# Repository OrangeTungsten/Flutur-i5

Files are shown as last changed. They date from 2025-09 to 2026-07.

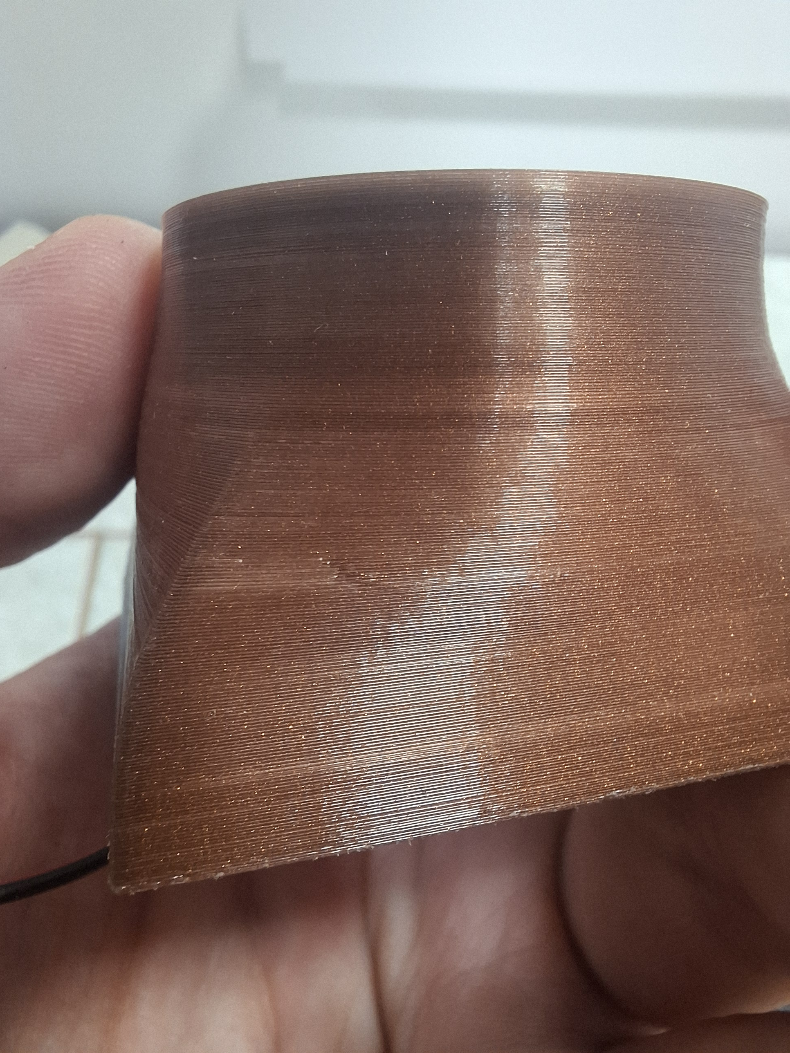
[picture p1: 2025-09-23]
Images/Printing results/20250920_120809.jpg

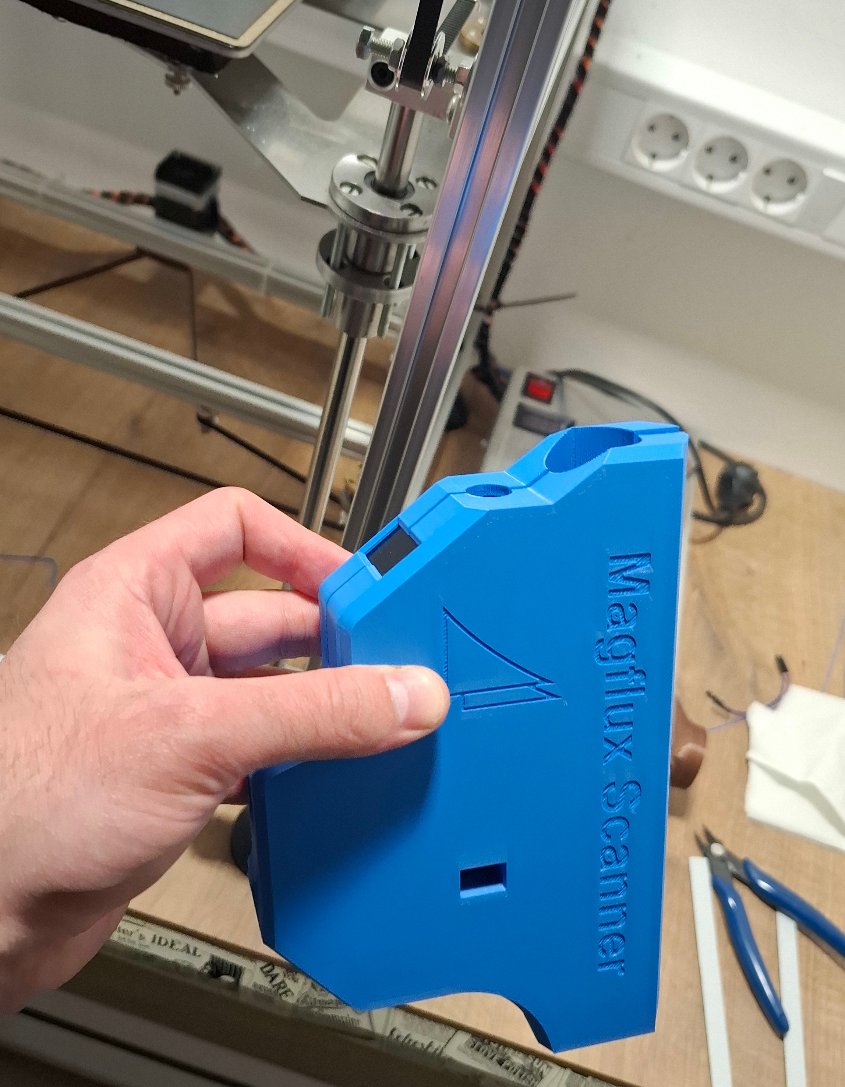
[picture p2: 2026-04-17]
Images/Printing results/11.jpg

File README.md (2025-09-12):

# Flutur-i5
Flutur Logo

# Introduction
Flutur i5 is an open-source 3D printer project, created by an enthusiast for the wider maker community. It is designed to inspire and support fellow makers and DIY lovers. The idea behind Flutur is to build a stable, reliable and flexibile 3D printer that is affordable, easy to assemble, operate and modify.

This is a 3D printer featuring a Cartesian-style positioning system, driven by three two-phase stepper motors: belt-driven on the X and Y axes, and lead screw-driven on the Z axis; all guided by linear bearings on Ø12 stainless steel rods. The entire system is assembled into a rigid rectangular (box-type) aluminum frame, made of 20 x 20 mm slot profile members. The printable volume is 285 × 300 × 300 mm (X × Y × Z).

# Bill of Materials (BOM)
The BOM.xls file contains materials with quantities needed for this project. Names of components follow provided assembly drawings. All measures are given in milimeters. 

Printable components could be FDM 3D printed with basic PLA filament, even the extruder plate. Both portal plates could be made of acrylics or aluminum. Hotend requires active cooling. Workpiece cooling is also recommended. 

In this version of the project, the control system consists of an _MKS Robin Nano v1.2_ control board, together with _TMC2208_ stepper drivers and a _MKS TFT35 v1.0_ display. The motion system is driven by four NEMA17 17HS8401 stepper motors. Power supply must provide at least 30 A at 12 V DC. The Flutur i5 project does not provide instructions for wiring or electrical instalation in general. The proper wiring, operation and handling of these components are defined by their respective manufacturers, and their official documentation should be followed.

The control board runs on [Marlin v2.1.2.5](https://github.com/MarlinFirmware/Marlin/tree/lts-2.1.2) firmware. Configuration files are given.

## 3rd Party Disclaimer

This project is designed to be compatible with certain commercially available components from third-party manufacturers. This project does not distribute, reproduce, or claim ownership of any third-party models. Users requiring detailed technical information, specifications, or official design files of these components, should obtain them directly from the respective manufacturers’ official sources. This project also uses a combination of widely available off-the-shelf components (e.g. standard bearings and fasteners). While references to such parts are made in the design, no third-party models are included in this repository.

The printer can also be realized with other solutions, depending on the builder’s preferences and requirements. In that case, modifications of certain parts may be required, such as adapting or redesigning mounting positions to fit the new hardware.

List of fully compatibile 3rd party components with their webistes:

[Stepper Motor NEMA17 17HS8401](https://www.hanpose.com/product-17hs8401-18a--52ncm-18-degree--linear--motor-12v-electric-toys-and-appliances-for-3d-printer-nema-17-stepper-motor)

[Controler board MKS Robin Nano v1.2](https://makerbase3d.com/product/mks-robin-nano-v1-2/)

[Display MKS TFT35 V1.0](https://makerbase3d.com/product/mks-robin-nano-v1-2/)

[Filament Feeder Creality MK8 style](https://www.crealityofficial.co.uk/products/full-metal-extruder-with-capricorn-tubing)

[Hotend E3D V6 type](https://e3d-online.com/products/v6-all-metal-hotend?_pos=5&_sid=d5b714545&_ss=r&variant=40923457486907)

[Sensor BL Touch v3.1](https://www.antclabs.com/bltouch)

[Endstop Cherry DB2 Microswitch](https://platinum-international.store/platinum-international/switches/position-switches/cherry-db2-subminiature-switch/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)

# Safety and Fire Hazard Disclaimer

3D printers are devices that operate with electricity and heat, and therefore must be considered potentially hazardous. Electrical wiring and installation on this device should only be performed by individuals with the appropriate knowledge and experience. Special attention must be given to all electrical connections, especially joints and connectors.

The author of this project assumes no responsibility or liability for any potential damage, injury, or loss resulting from the reproduction, assembly, or use of this device. All responsibility rests with the builder/user.

Building your own 3D printer can be a fun and rewarding experience, but please remember: safety comes first. Always double-check your wiring, use quality connectors, and don’t leave the printer unattended during operation. Treat this project as both a learning journey and a responsibility — careful assembly and mindful use will make your device safer and more reliable.

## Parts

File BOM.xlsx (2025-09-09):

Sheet: All Total
Item | Qty.
Aluminum Profiles
Slot Profile 2020 l = 525 | 4
Slot Profile 2020 l = 410 | 6
Slot Profile 2020 l = 480 | 5
Profile Connectors
Slot Profile Corner Connector | 4
Slot Profile Angle Connector | 6
Slot Profile Angle Connector-Short | 4
Slot Profile Plate Connector | 8
External Angle Connector | 12
T Slot Nut 2020 M5 | 89
Adjustable Leg M5 | 4
Motion
Stepper Motor NEMA17 17HS8401 | 4
Synchronous Pulley GT2-20t x 6 | 6
Synchronous Pulley GT2-40t x 6 | 2
Idler Pulley GT2-20t x 6 | 9
Synchronous Loop Belt GT2-158 x 6 | 1
Synchronous Loop Belt GT2-1220 x 6 | 1
Synchronous Belt GT2-1116 x 6 | 1
Synchronous Belt GT2-970 x 6 | 2
Ball Bearing F686-2RS 6 x 13 x 5 | 2
Y Shaft Φ6 x 515 | 1
Linear Guide Support SK12 | 16
Linear Guide Φ12 x 370 | 4
Linear Guide Φ12 x 446 | 2
Linear Guide Φ12 x 375 | 2
Linear Bearing Block SC12UU | 6
Linear Bearing Block LMF12UU | 4
Ball Bearing with Housing KP08 | 2
Lead Screw T10 x 2 | 2
Lead Nut T10 x 2 | 2
Fasteners
Cross Head Screw M2 x 14 | 4
Nut M2 | 4
Washer 2.5x5x0.5 | 4
Cross Head Screw M3 x 6 | 44
Cross Head Screw M3 x 12 | 18
Cross Head Countersink Bolt M3 x 10 | 12
Cross Head Countersink Bolt M3 x 40 | 4
Nut M3 | 18
Knob Nut M3 | 4
Insert Nut M3 x 3 | 30
Washer 3.5 x 7 x 0.5 | 22
Flat Head Bolt M4 x 10 | 23
Nut M4 | 21
Insert Nut M4 x 4 | 4
Washer 4.5 x 9 x 0.8 | 19
Cross Head Bolt M5 x 10 | 49
Cross Head Bolt M5 x 12 | 62
Cross Head Screw M5 x 35 | 2
Socket Head Bolt M5 x 30 | 8
Hexagonal Head Bolt M5 x 35 | 11
Nut M5 | 29
Washer 5.5 x 10 x 1.5 | 8
Washer 5.5x15x1.5 | 8
Washer 5.5 x 18 x 1.5 | 11
Idler Pulley Positioner | 22
Compression Spring 20 x 5 x 5 | 4
Printables
Extruder plate | 1
Stepper Motor Bracket | 2
Portal Plate - Right | 1
Portal Plate - Left | 1
Y Shaft Bearing Bracket | 2
Cable Bracket - Right | 1
Cable Bracket - Left | 1
Cable Bracket - Extruder | 1
Y Endstop Spacer | 1
Belt Pin | 4
Bl Touch Bracket | 1
Housing Leg | 4
Front Panel Holder | 1
Display Panel | 1
Side Fan Holder | 2
Upper Fan Holder | 1
Electro-mechanical
Endstop Cherry DB2 Microswitch | 2
BL Touch v3.1 | 1
Main Switch 250V 10A 22 x 28 | 1
Reset Push-button Ø6 | 1
Fan Ø40 | 4
Power Supply 320 W | 1
Controller Board | 1
Display | 1
Sheet metal work
Filament Feeder Plate | 1
Heated Bed Plate | 1
Housing Base | 1
Housing Lid | 1
Material Deposition
Filament Feeder MK8-style | 1
Teflon Tube Φ1.75 x 120 | 1
Hotend E3D V6 type | 1
Aluminum Heated Bed 310 x 310 | 1
Cable management
Flat Bar Connector 20 x 458.5 x 4 | 1
X Cable Chain Rail 10 x 15 x 400 | 1
Y Cable Chain Rail 10 x 15 x 400 | 2
Z Cable Chain Rail 10 x 15 x 400 | 1
Cables
2 x 0.14 (20 AWG) x 2400 | 1
4 x 0.14 (26 AWG) x 1600 | 1
4 x 0.25 (23 AWG) x 1600 | 1
2 x 0.35 (22 AWG) x 3200 | 1
4 x 0.5 (20 AWG) x 3800 | 1
2 x 0.75 (18 AWG) x 1600 | 1
2 x 2.5 (14 AWG) x 800 | 1

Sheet: Cables
No. | Purpose | Cores | CS [mm2] | AWG | Qty. | Length [m] | Note
1 | Stepper E | 4 | 0.50 | 20 | 1 | 1.6
2 | Heater - E | 2 | 0.75 | 18 | 1 | 1.6 | Heat-resistant insulation
3 | Thermistor | 2 | 0.14 | 26 | 1 | 1.6
4 | Fans | 2 | 0.35 | 22 | 2 | 1.6
5 | BL Touch | 4 | 0.14 | 26 | 1 | 1.6
6 | Stepper X | 4 | 0.50 | 20 | 1 | 1.6
7 | Endstops | 4 | 0.25 | 23 | 1 | 1.6
8 | Heater - HB | 2 | 2.50 | 14 | 1 | 0.8 | Heat-resistant insulation
9 | Thermistor | 2 | 0.14 | 26 | 1 | 0.8
10 | Stepper Y | 4 | 0.50 | 20 | 1 | 1.2
11 | Stepper Z | 4 | 0.50 | 20 | 1 | 0.6
Total
Cores | CS [mm2] | AWG | Length [m]
2 | 0.14 | 26 | 2.4
4 | 0.14 | 26 | 1.6
4 | 0.25 | 23 | 1.6
2 | 0.35 | 22 | 3.2
4 | 0.50 | 20 | 3.8
2 | 0.75 | 18 | 1.6
2 | 2.50 | 14 | 0.8

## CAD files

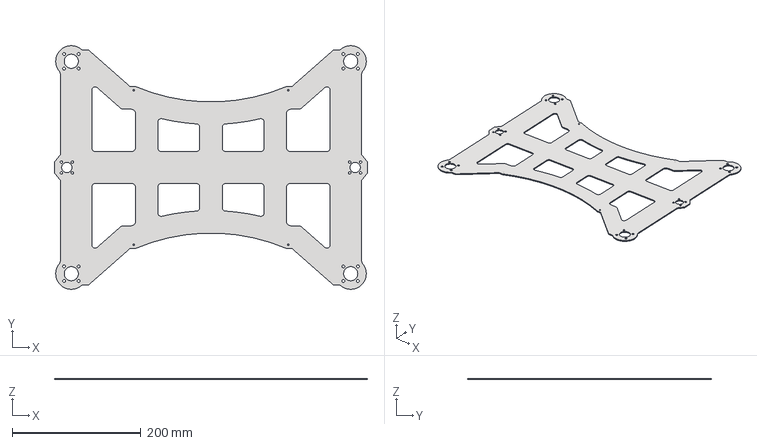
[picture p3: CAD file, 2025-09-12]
CAD/STEP/Heated bed plate.stp
486.3 x 378.5 x 2.00 mm

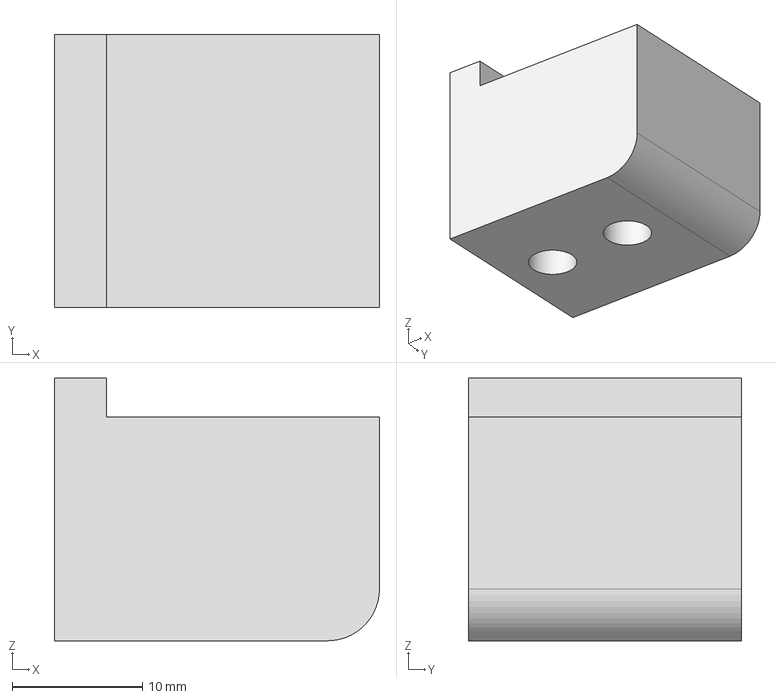
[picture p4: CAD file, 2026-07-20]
CAD/STEP/Housing/microSD Holder.stp
25.0 x 21.0 x 20.2 mm

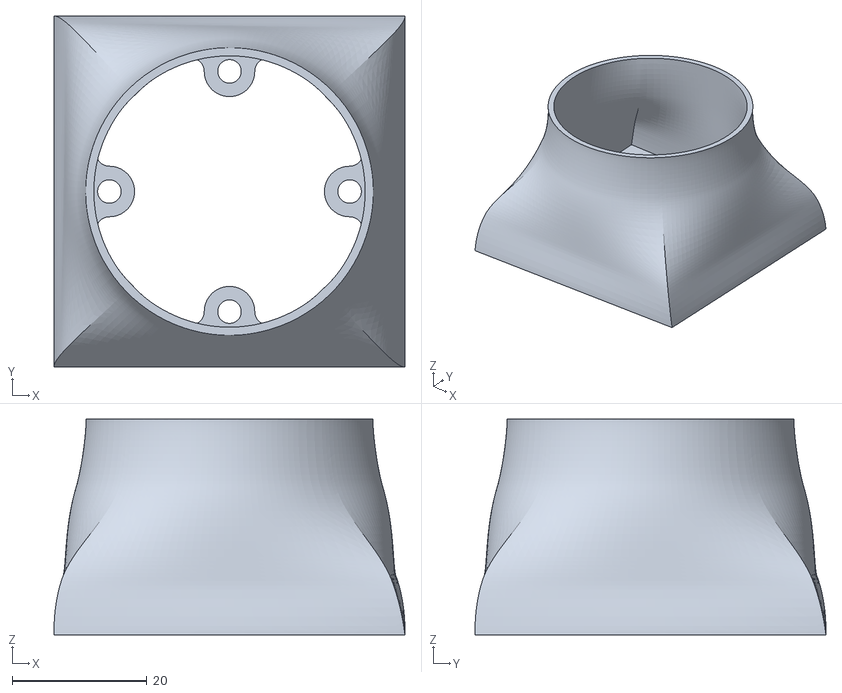
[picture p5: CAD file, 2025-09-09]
CAD/STL/Housing/Side fan holder.stl
52.0 x 52.0 x 32.0

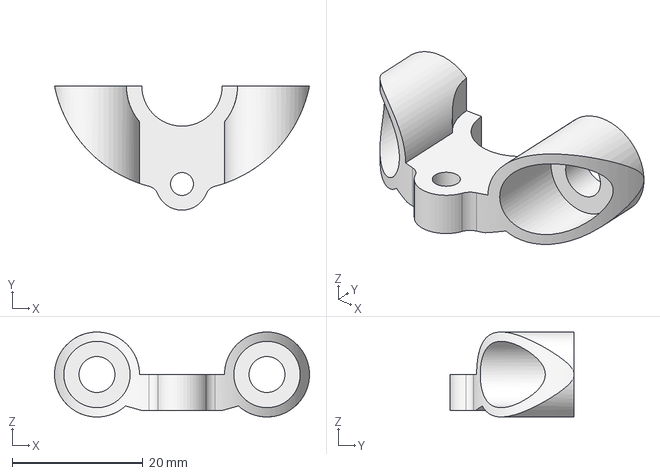
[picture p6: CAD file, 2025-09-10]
CAD/STEP/Extruder plate-cap.stp
39.0 x 19.0 x 13.0 mm

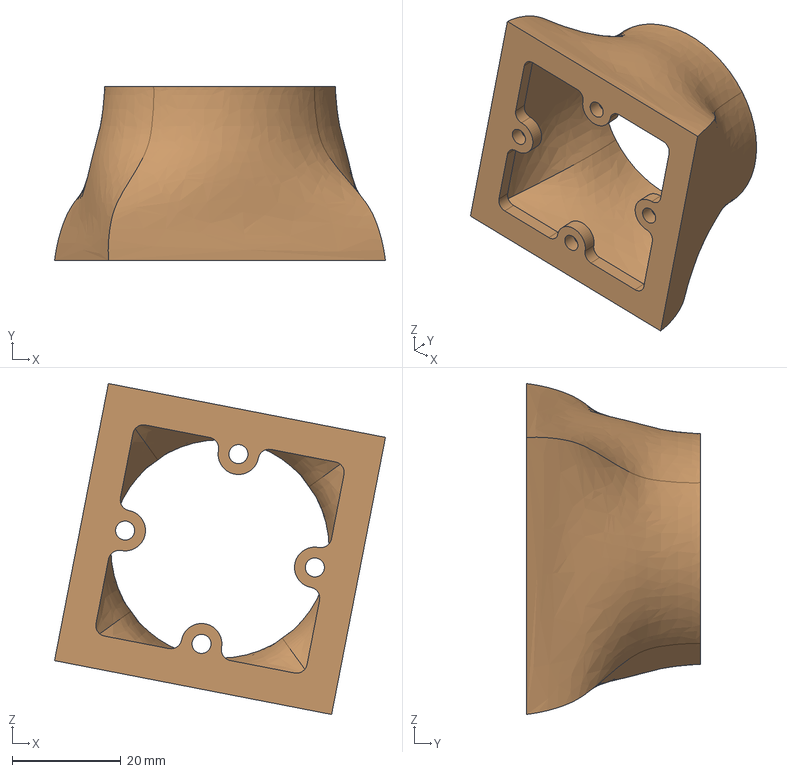
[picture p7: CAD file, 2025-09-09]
CAD/STEP/Housing/Side fan bracket.stp
61.0 x 32.0 x 61.0 mm

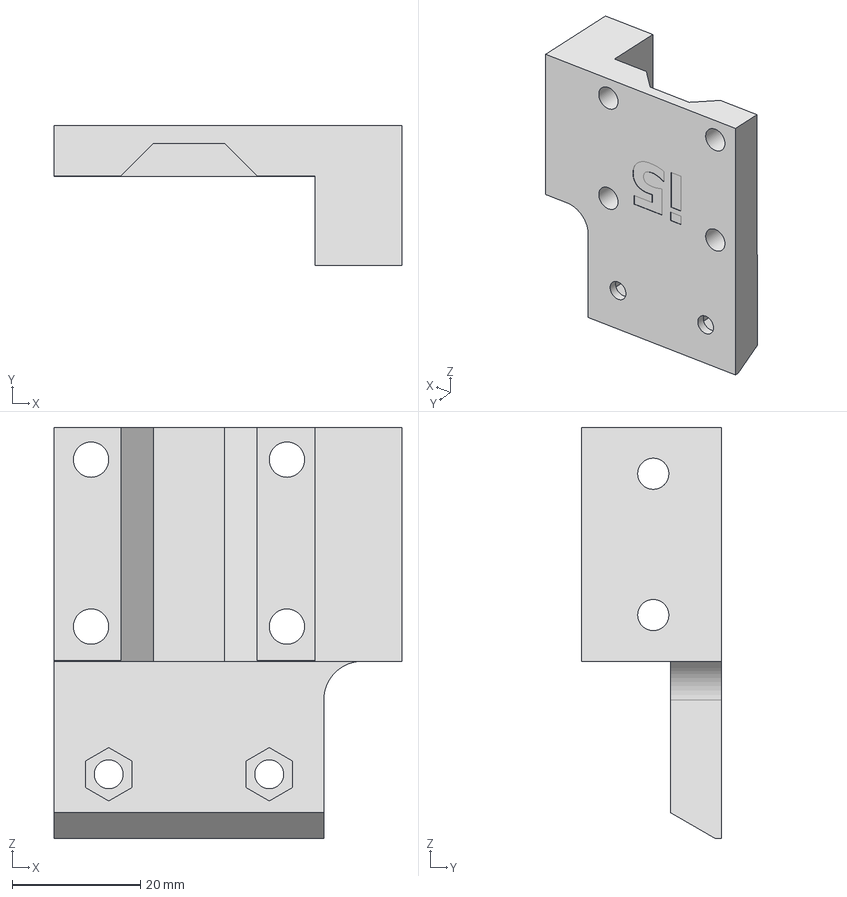
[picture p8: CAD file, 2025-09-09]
CAD/STEP/Cable bracket-right.stp
54.2 x 21.9 x 64.0 mm

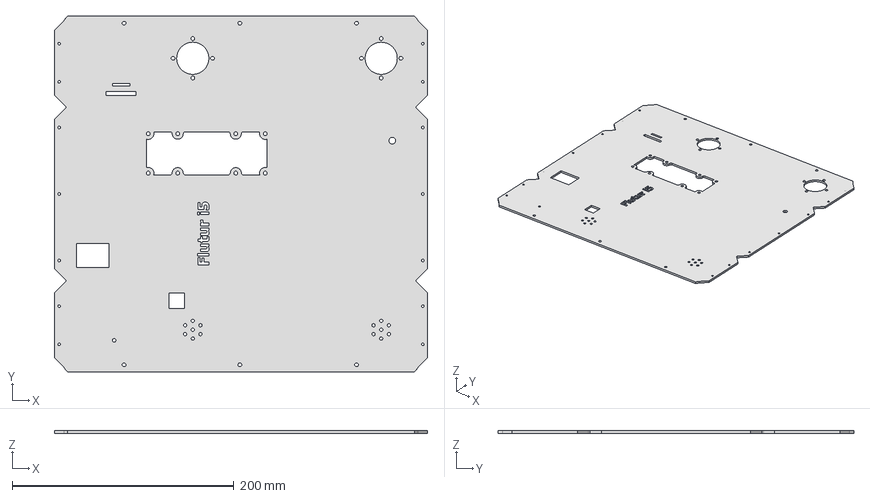
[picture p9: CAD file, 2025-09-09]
CAD/STEP/Housing/Housing Lid-flat.stp
336.6 x 321.2 x 2.50 mm

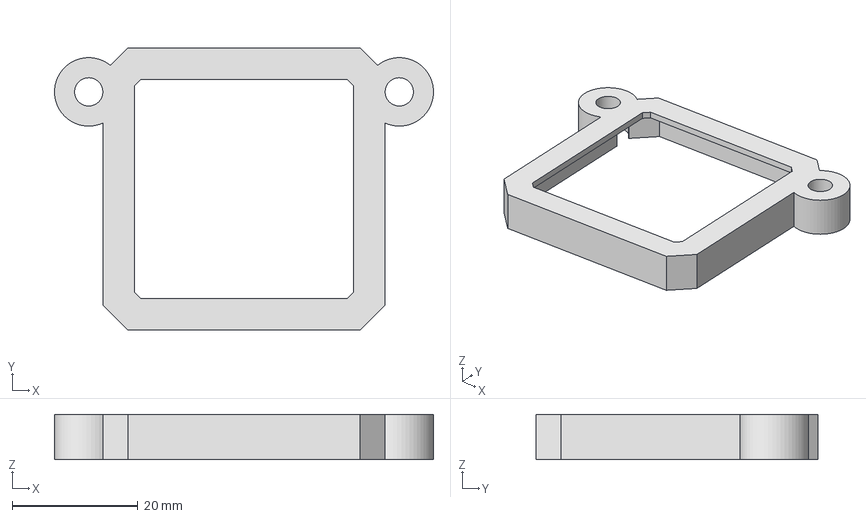
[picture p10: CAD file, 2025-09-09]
CAD/STEP/Cable bracket-extruder.stp
60.3 x 44.9 x 7.20 mm

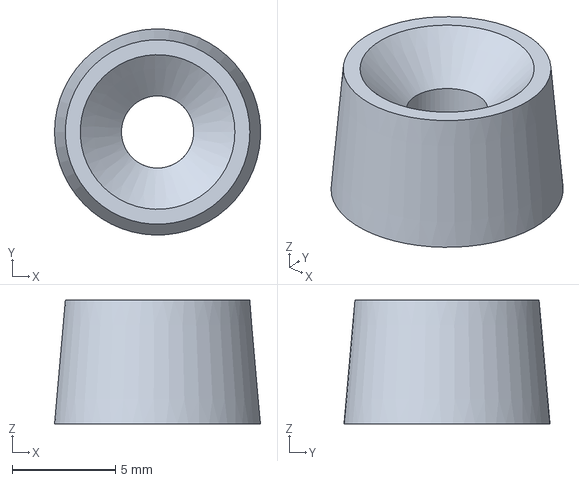
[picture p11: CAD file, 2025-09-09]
CAD/STEP/Housing/Leg.stp
9.99 x 10.00 x 6.00 mm

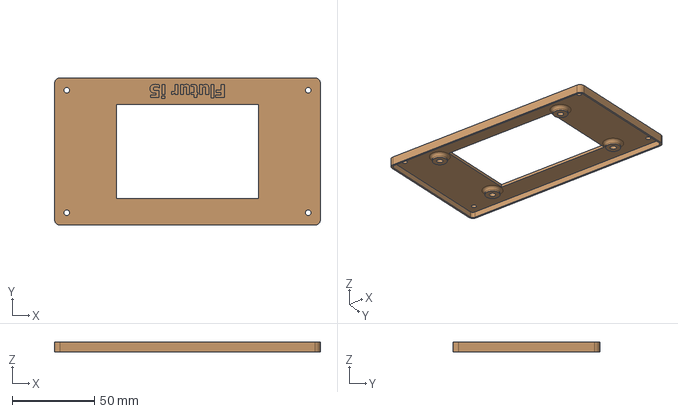
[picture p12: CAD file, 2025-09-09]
CAD/STEP/Housing/Display panel.stp
161.8 x 89.6 x 6.00 mm

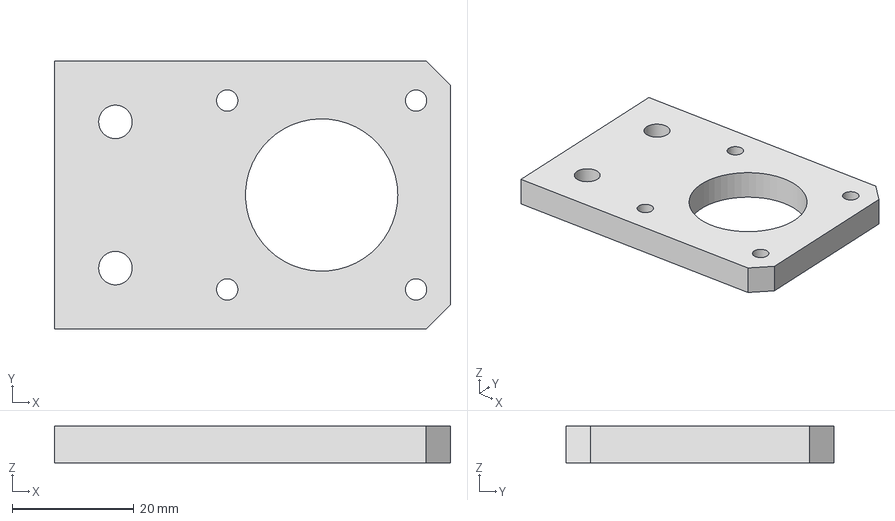
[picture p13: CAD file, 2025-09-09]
CAD/STEP/Stepper motor bracket.stp
65.0 x 44.0 x 6.00 mm

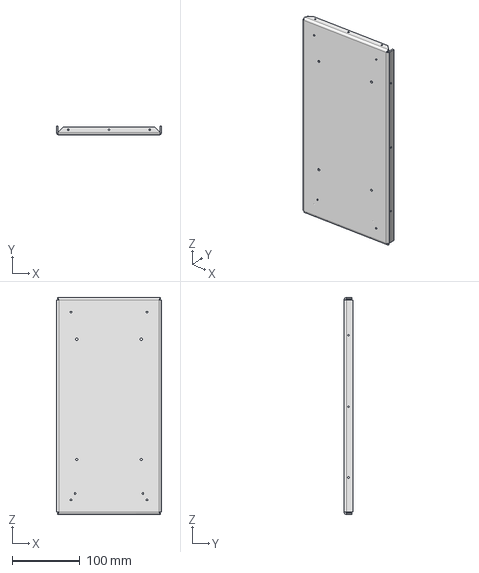
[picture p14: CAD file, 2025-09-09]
CAD/STEP/Housing/Housing base-folded.stp
155.0 x 13.0 x 320.0 mm

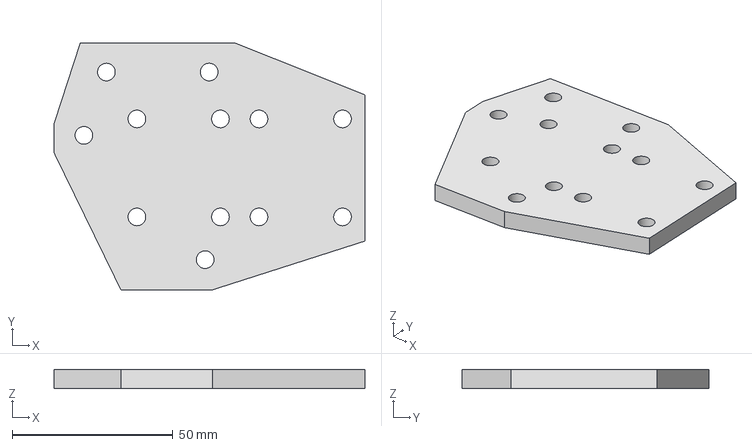
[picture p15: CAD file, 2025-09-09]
CAD/STEP/Portal plate-right.stp
96.8 x 76.8 x 6.00 mm

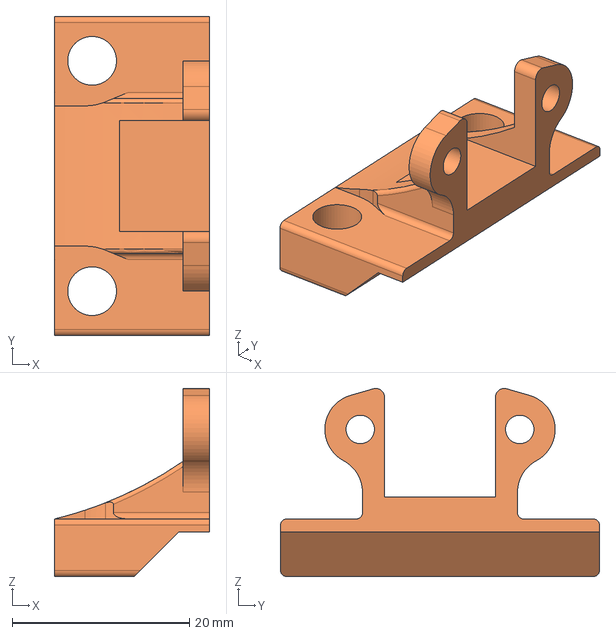
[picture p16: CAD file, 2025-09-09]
CAD/STEP/BL Touch bracket.stp
17.5 x 36.0 x 21.2 mm

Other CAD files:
CAD/STEP/Housing/Front panel holder.stp
CAD/STEP/Housing/Housing Lid-folded.stp
CAD/STEP/Portal plate-left.stp
CAD/STEP/Housing/Upper fan bracket.stp
CAD/STEP/Belt pin.stp
CAD/STEP/Cable bracket-left.stp
CAD/STEP/Extruder plate.stp
CAD/STEP/Filament Feeder Plate.stp
CAD/STEP/Housing/Housing base-flat.stp
CAD/STEP/Housing/Upper fan bracket-cap.stp
CAD/STEP/Y Endstop spacer.stp
CAD/STEP/Y Shaft bearing bracket.stp
CAD/STL/BL Touch bracket.stl
CAD/STL/Belt pin.stl
CAD/STL/Cable bracket-extruder.stl
CAD/STL/Cable bracket-left.stl
CAD/STL/Cable bracket-right.stl
CAD/STL/Extruder plate-cap.stl
CAD/STL/Extruder plate.stl
CAD/STL/Filament Feeder Plate.stl
CAD/STL/Housing/Display panel.stl
CAD/STL/Housing/Front panel holder.stl
CAD/STL/Housing/Leg.stl
CAD/STL/Housing/Upper fan bracket-cap.stl
CAD/STL/Housing/Upper fan bracket.stl
CAD/STL/Housing/microSD Holder.stl
CAD/STL/Portal plate-left.stl
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

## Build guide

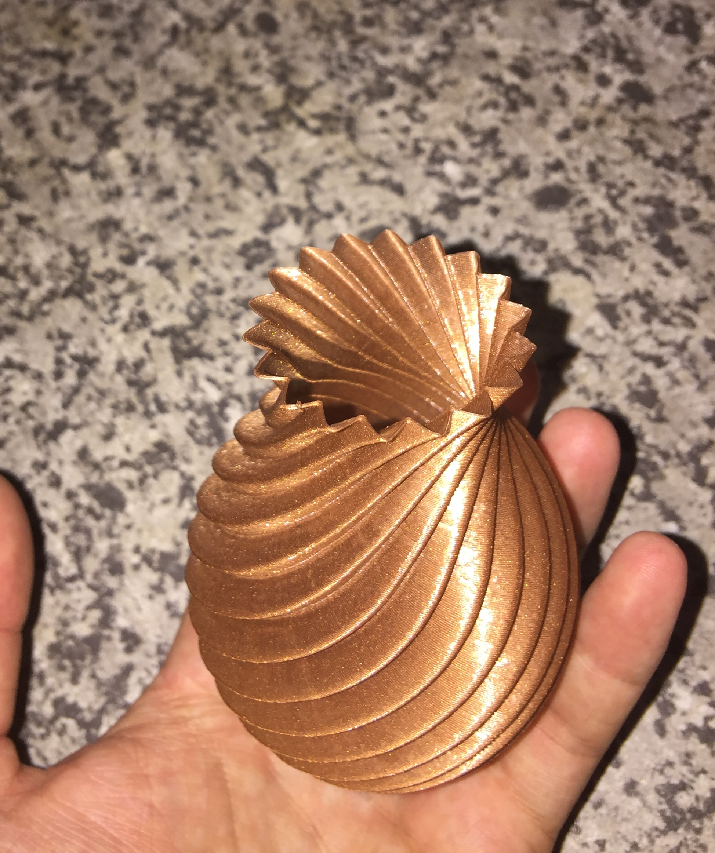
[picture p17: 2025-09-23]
Images/Printing results/2.JPG

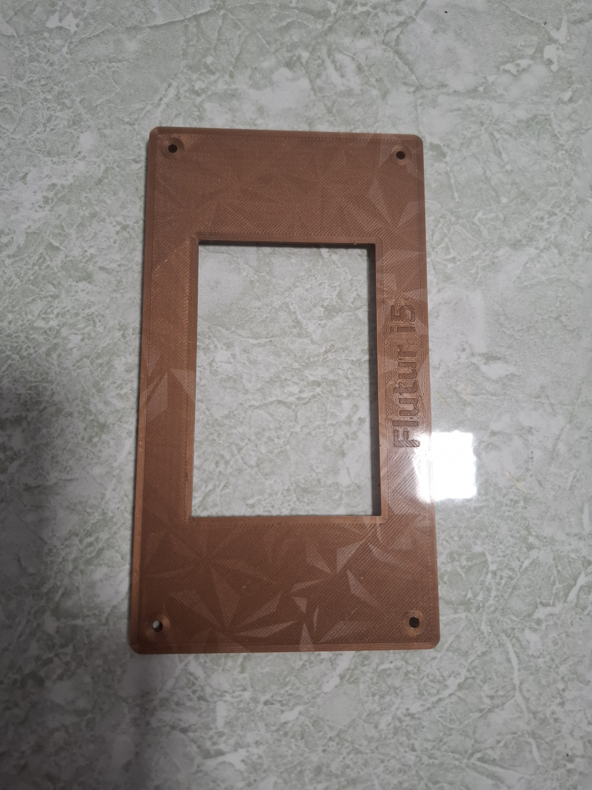
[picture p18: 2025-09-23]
Images/Printing results/8.jpg

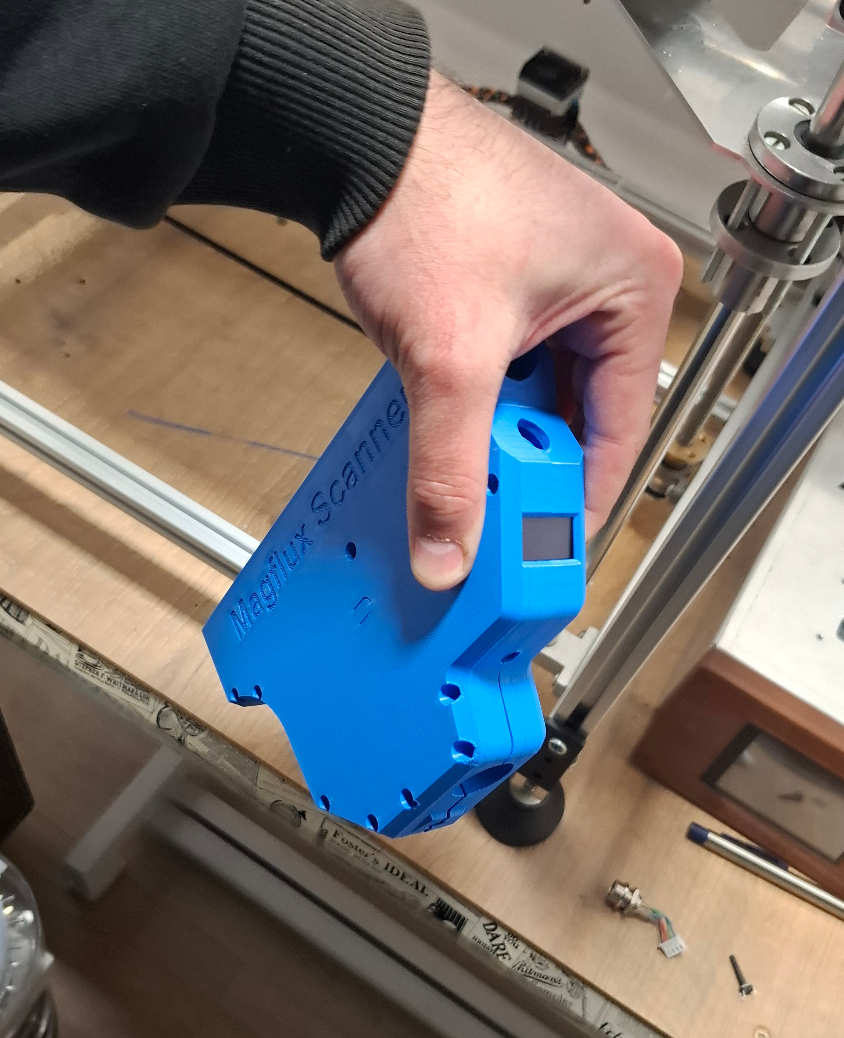
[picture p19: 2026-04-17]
Images/Printing results/10.jpg

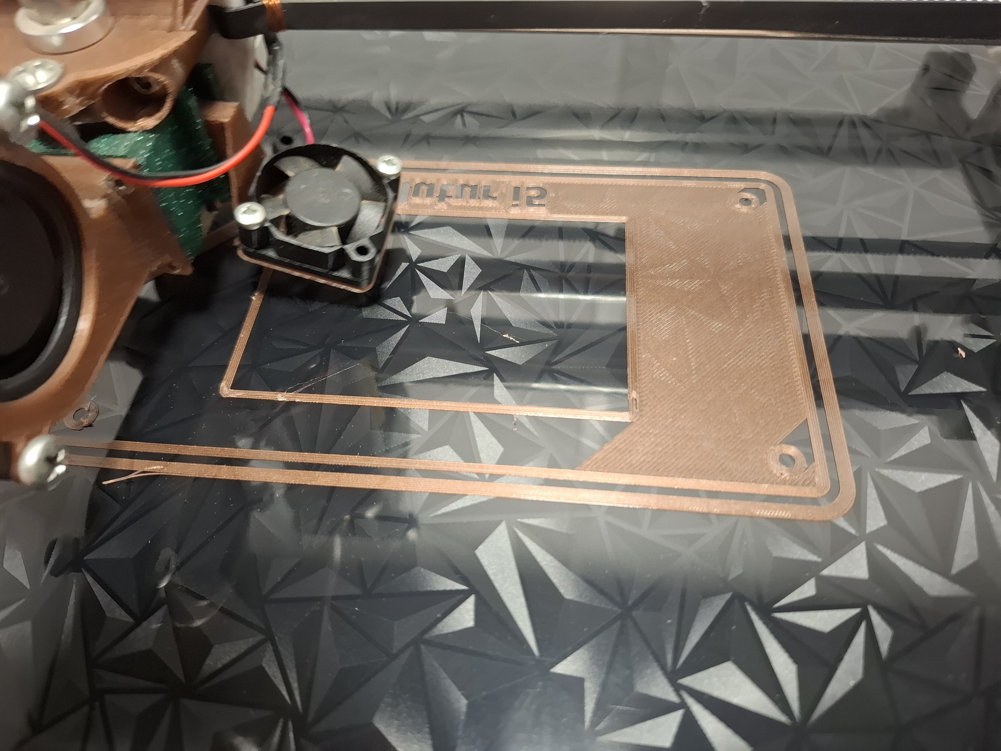
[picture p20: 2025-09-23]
Images/Printing results/9.jpg

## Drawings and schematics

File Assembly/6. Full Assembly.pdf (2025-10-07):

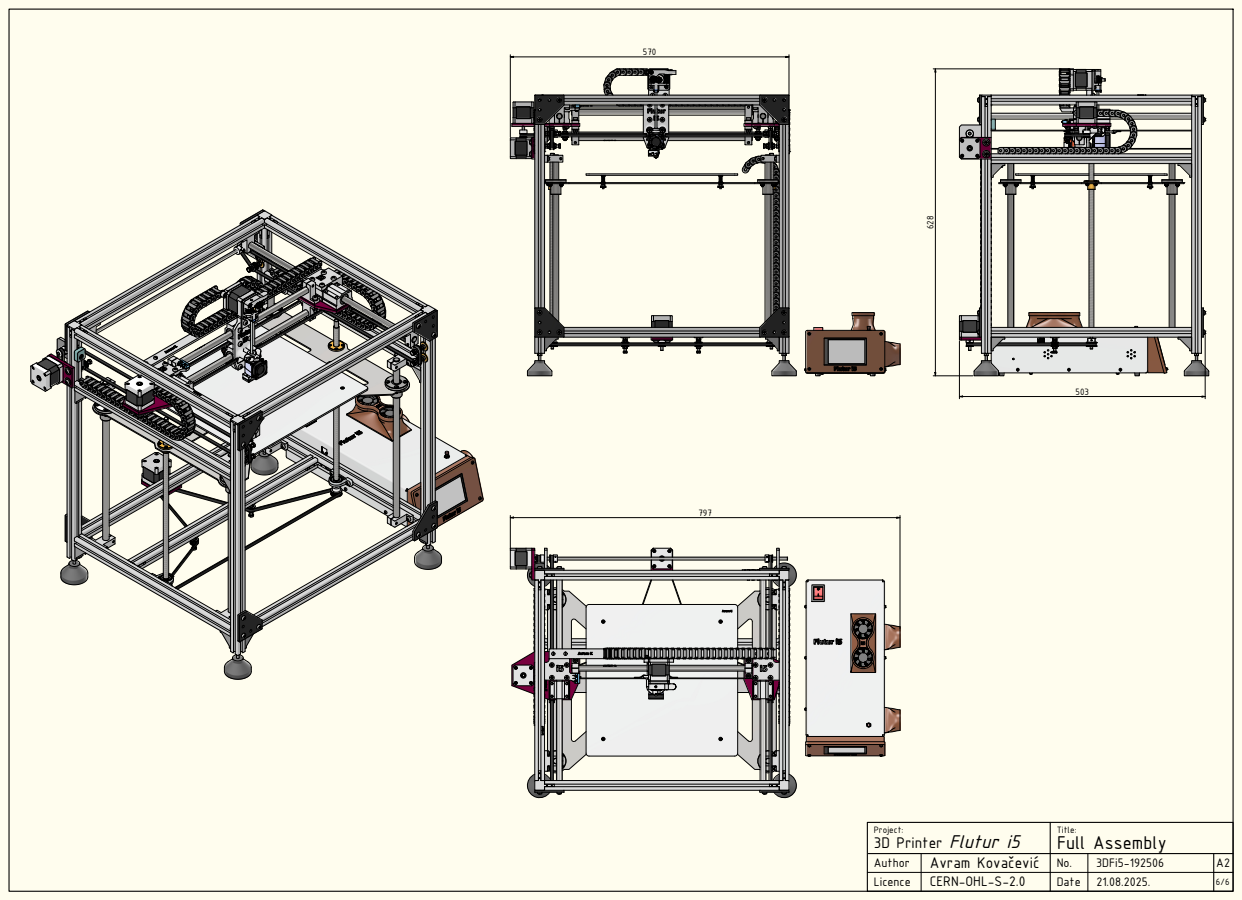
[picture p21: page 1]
Avram Kovačević; 3D Printer Flutur i5; Full Assembly

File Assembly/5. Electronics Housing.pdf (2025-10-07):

82

89

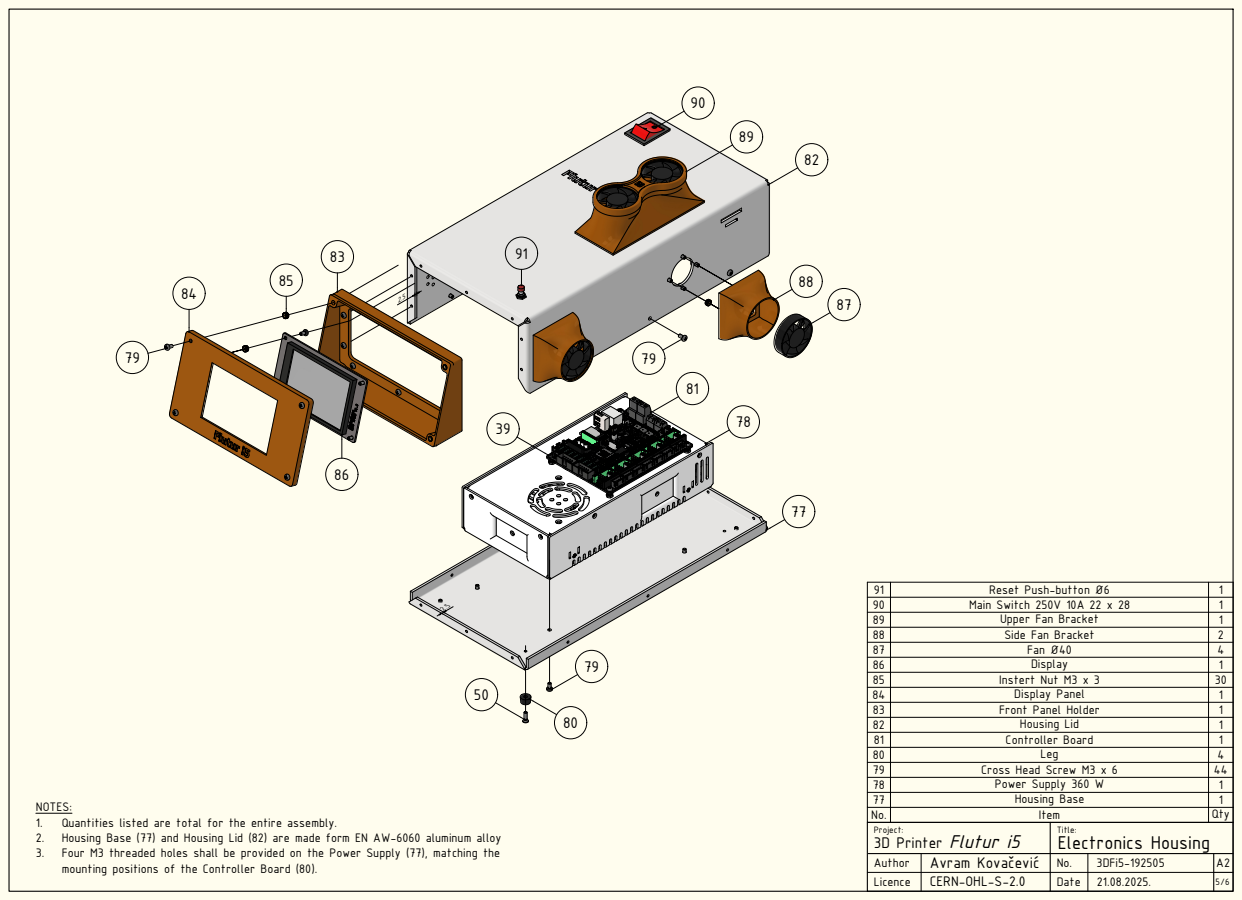
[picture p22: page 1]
Project:; Title:; Author; Licence; Avram Kovačević; 3D Printer Flutur i5; CERN-OHL-S-2.0; Date; 3DFi5-192505; Electronics Housing; Reset Push-button Ø6; Main Switch 250V 10A 22 x 28; Upper Fan Bracket; Side Fan Bracket; Fan Ø40; Display; Instert Nut M3 x 3; Display Panel; Front Panel Holder; Housing Lid; Controller Board; Leg; Cross Head Screw M3 x 6; Power Supply 360 W; Housing Base; Item; Qty NOTES:

1. Quantities listed are total for the entire assembly.
2. Housing Base (77) and Housing Lid (82) are made form EN AW-6060 aluminum alloy
3. Four M3 threaded holes shall be provided on the Power Supply (77), matching the
mounting positions of the Controller Board (80).

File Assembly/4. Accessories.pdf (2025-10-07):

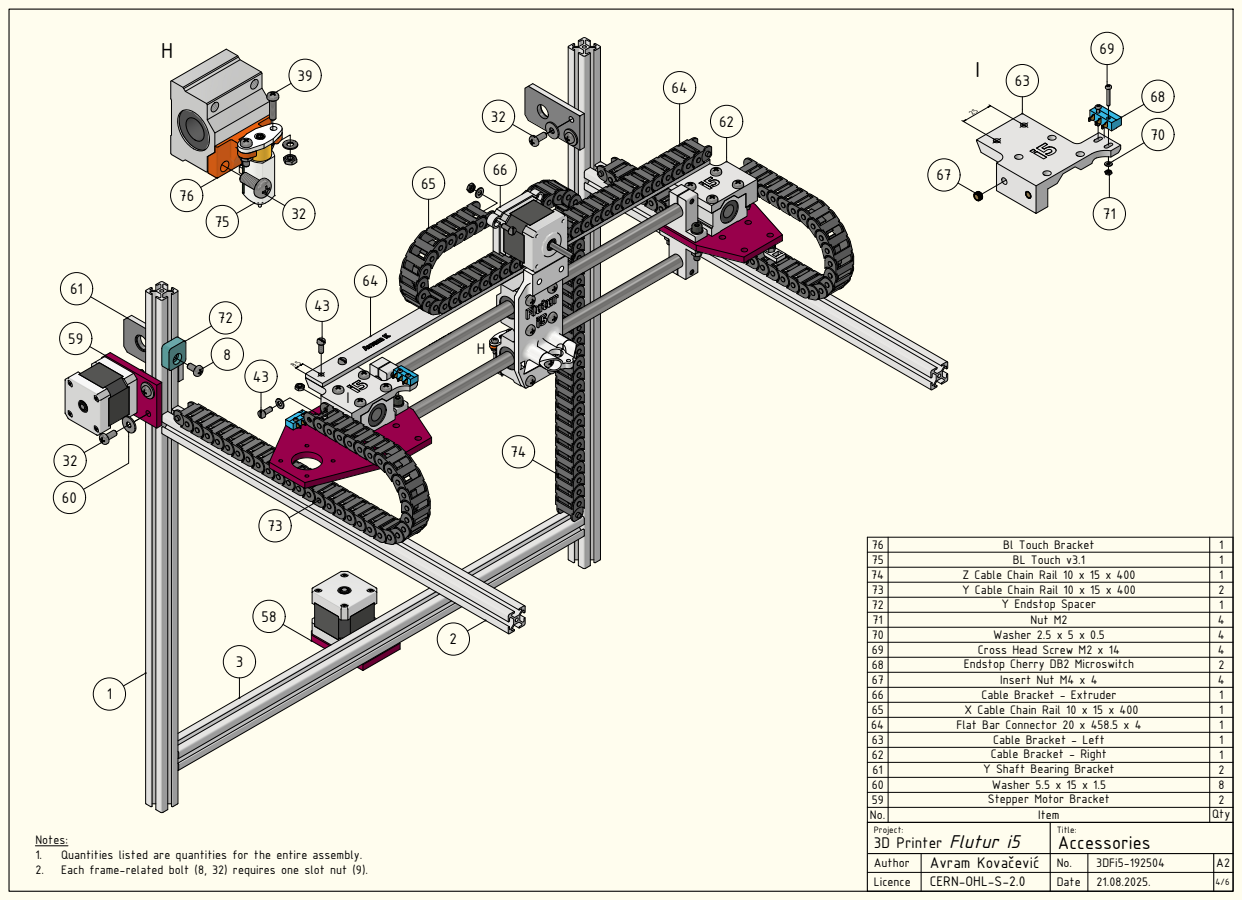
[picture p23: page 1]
Avram Kova; 3D Printer Flutur i5; Bl Touch Bracket; BL Touch v3.1; Z Cable Chain Rail 10 x 15 x 400; Y Cable Chain Rail 10 x 15 x 400; Y Endstop Spacer; Nut M2; Washer 2.5 x 5 x 0.5; Cross Head Screw M2 x 14; Endstop Cherry DB2 Microswitch; Insert Nut M4 x 4; Cable Bracket - Extruder; X Cable Chain Rail 10 x 15 x 400; Flat Bar Connector 20 x 458.5 x 4; Cable Bracket - Left; Cable Bracket - Right; Y Shaft Bearing Bracket; Washer 5.5 x 15 x 1.5; Stepper Motor Bracket

Notes:
1. Quantities listed are quantities for the entire assembly.
2. Each frame-related bolt (8, 32) requires one slot nut (9).

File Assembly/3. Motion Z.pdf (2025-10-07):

48

47

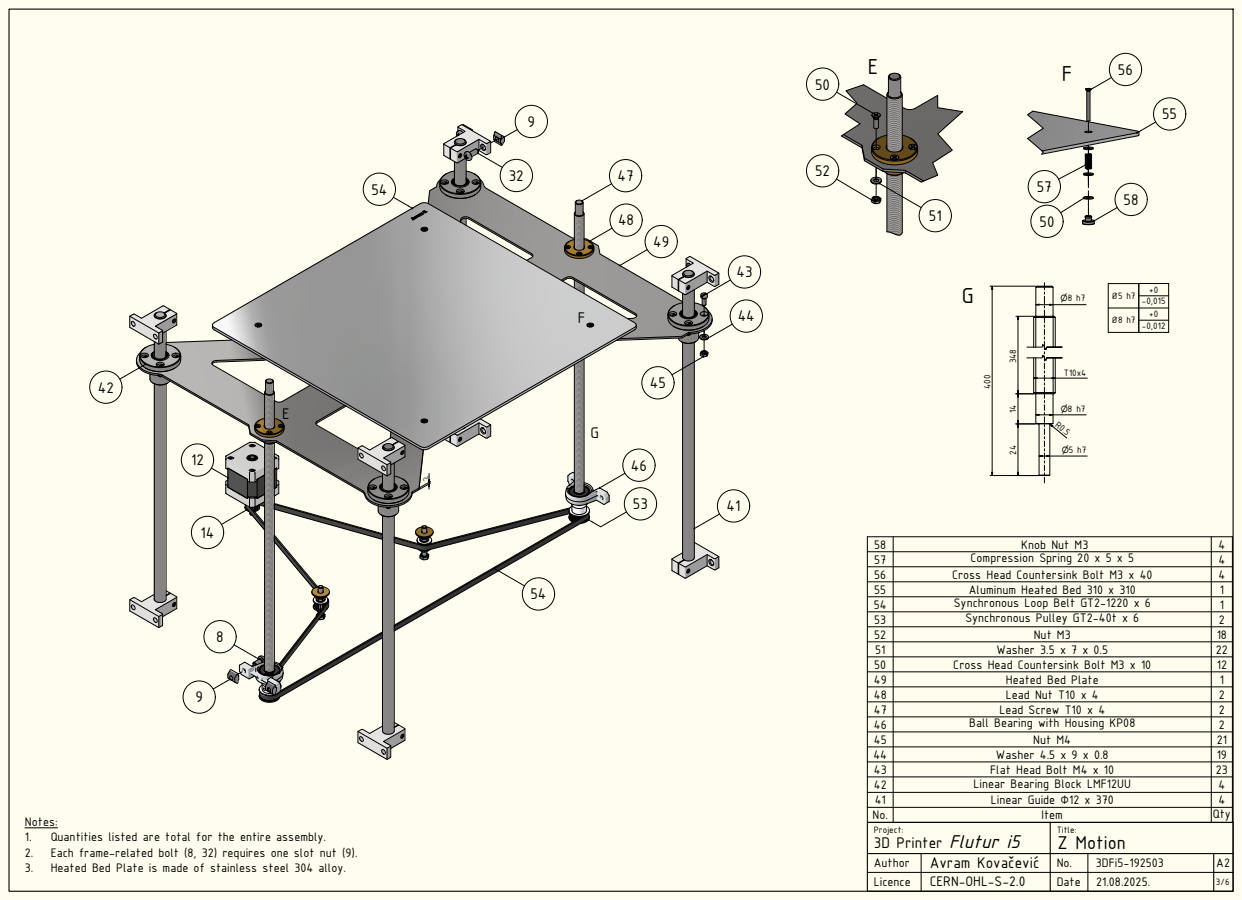
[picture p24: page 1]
Project:; Title:; Author; Licence; Avram Kovačević; 3D Printer Flutur i5; CERN-OHL-S-2.0; Date; Knob Nut M3; Compression Spring 20 x 5 x 5; Cross Head Countersink Bolt M3 x 40; Aluminum Heated Bed 310 x 310; Synchronous Loop Belt GT2-1220 x 6; Synchronous Pulley GT2-40t x 6; Nut M3; Washer 3.5 x 7 x 0.5; Cross Head Countersink Bolt M3 x 10; Heated Bed Plate; Lead Nut T10 x 4; Lead Screw T10 x 4; Ball Bearing with Housing KP08; Nut M4; Washer 4.5 x 9 x 0.8; Flat Head Bolt M4 x 10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

Notes:
1. Quantities listed are total for the entire assembly.
2. Each frame-related bolt (8, 32) requires one slot nut (9).
3. Heated Bed Plate is made of stainless steel 304 alloy.

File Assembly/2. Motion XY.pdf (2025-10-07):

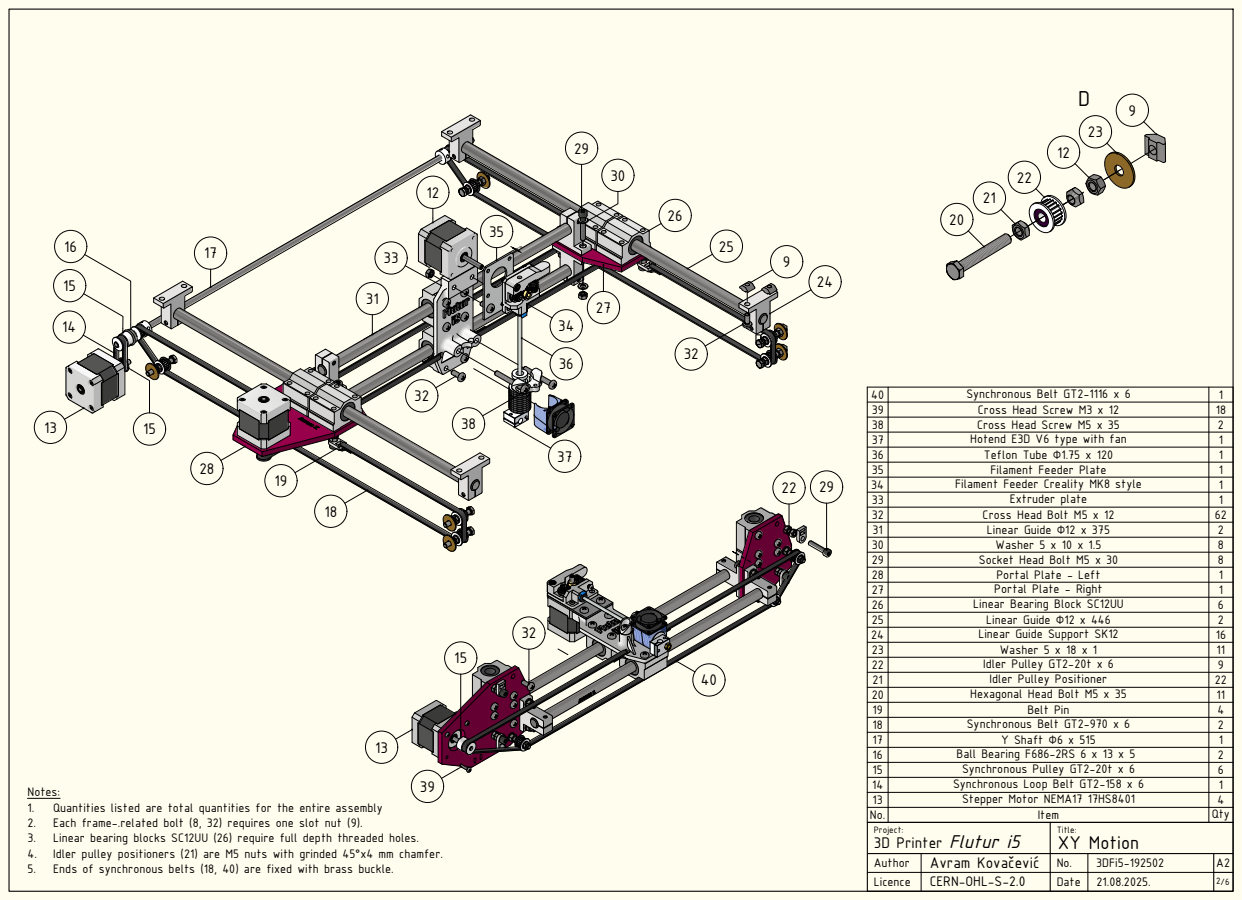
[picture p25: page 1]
°x4 mm chamfer.

40 | Synchronous Belt GT2-1116 x 6 | 1
39 | Cross Head Screw M3 x 12 | 18
38 | Cross Head Screw M5 x 35 | 2
37 | Hotend E3D V6 type with fan | 1
36 | Teflon Tube Φ1.75 x 120 | 1
35 | Filament Feeder Plate | 1
34 | Filament Feeder Creality MK8 style | 1
33 | Extruder plate | 1
32 | Cross Head Bolt M5 x 12 | 62
31 | Linear Guide Φ12 x 375 | 2
30 | Washer 5 x 10 x 1.5 | 8
29 | Socket Head Bolt M5 x 30 | 8
28 | Portal Plate - Left | 1
27 | Portal Plate - Right | 1
26 | Linear Bearing Block SC12UU | 6
25 | Linear Guide Φ12 x 446 | 2
24 | Linear Guide Support SK12 | 16
23 | Washer 5 x 18 x 1 | 11
22 | Idler Pulley GT2-20t x 6 | 9
21 | Idler Pulley Positioner | 22
20 | Hexagonal Head Bolt M5 x 35 | 11
19 | Belt Pin | 4
18 | Synchronous Belt GT2-970 x 6 | 2
17 | Y Shaft Φ6 x 515 | 1
16 | Ball Bearing F686-2RS 6 x 13 x 5 | 2
15 | Synchronous Pulley GT2-20t x 6 | 6
14 | Synchronous Loop Belt GT2-158 x 6 | 1
13 | Stepper Motor NEMA17 17HS8401 | 4
No. | Item | Qty

Notes:
1. Quantities listed are total quantities for the entire assembly
2. Each frame-.related bolt (8, 32) requires one slot nut (9).
3. Linear bearing blocks SC12UU (26) require full depth threaded holes.
4. Idler pulley positioners (21) are M5 nuts with grinded 45
5. Ends of synchronous belts (18, 40) are fixed with brass buckle.

Project: 3D Printer Flutur i5 | Title: XY Motion

Author | Avram Kova čevi ć | No. | 3DFi5-192502 | A2
Licence | CERN-OHL-S-2.0 | Date | 21.08.2025. | 2 /6

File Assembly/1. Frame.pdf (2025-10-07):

A

B

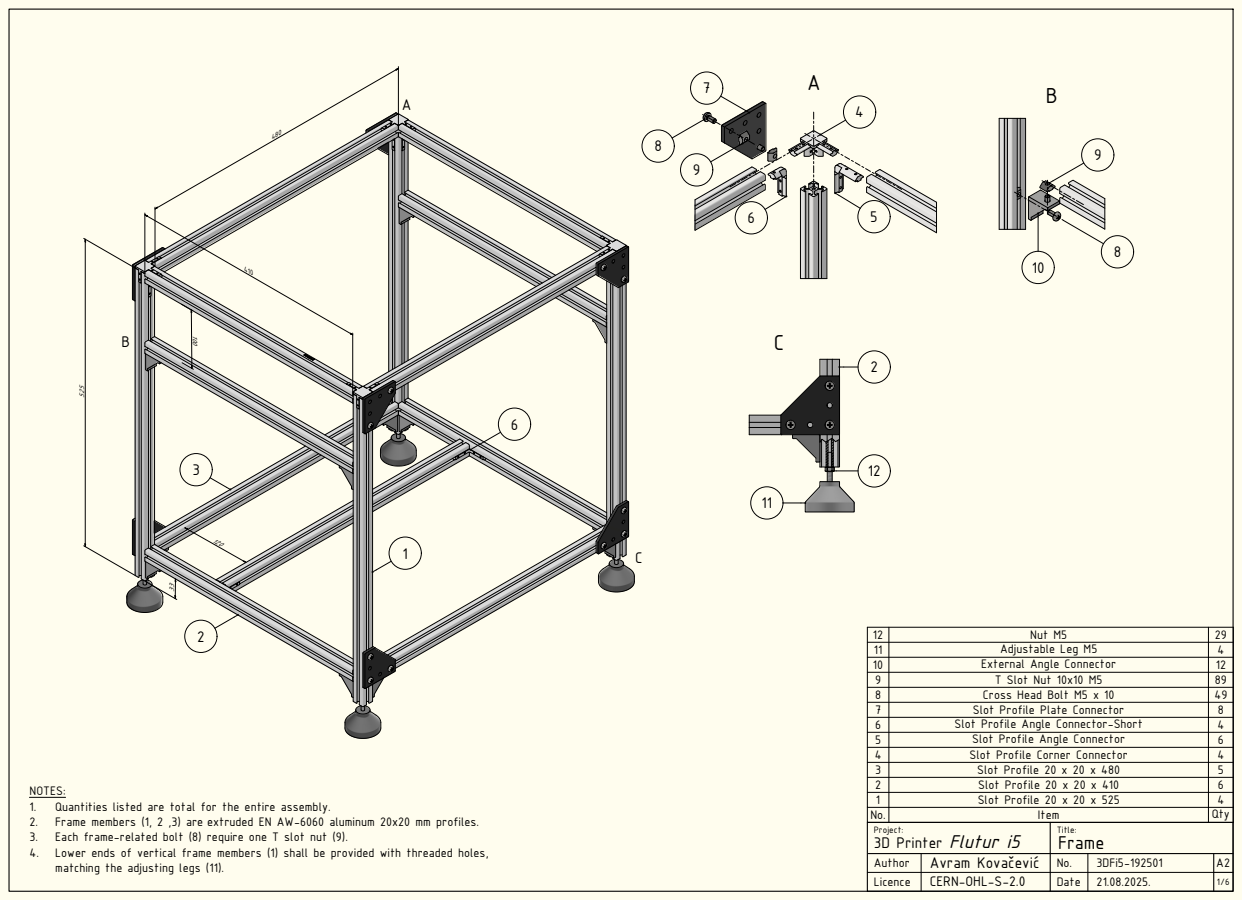
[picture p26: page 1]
Project:; Title:; Author; Licence; Avram Kovačević; 3D Printer Flutur i5; CERN-OHL-S-2.0; Date; Nut M5; Adjustable Leg M5; External Angle Connector; T Slot Nut 10x10 M5; Cross Head Bolt M5 x 10; Slot Profile Plate Connector; Slot Profile Angle Connector-Short; Slot Profile Angle Connector; Slot Profile Corner Connector; Slot Profile 20 x 20 x 480; Slot Profile 20 x 20 x 410; Slot Profile 20 x 20 x 525; Item; Qty; Frame; 3DFi5-192501

NOTES:
1. Quantities listed are total for the entire assembly.
2. Frame members (1, 2 ,3) are extruded EN AW-6060 aluminum 20x20 mm profiles.
3. Each frame-related bolt (8) require one T slot nut (9).
4. Lower ends of vertical frame members (1) shall be provided with threaded holes,
matching the adjusting legs (11).

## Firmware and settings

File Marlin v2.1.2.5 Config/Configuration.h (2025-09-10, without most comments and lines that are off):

#pragma once
#define CONFIGURATION_H_VERSION 02010205
#define STRING_CONFIG_H_AUTHOR "Avram Kovacevic" // Who made the changes.
#define SHOW_BOOTSCREEN
  #define MOTHERBOARD BOARD_MKS_ROBIN_NANO
#define SERIAL_PORT 3 //UART3 Tx=PB10/Rx=PB11
#define BAUDRATE 250000
#define CUSTOM_MACHINE_NAME "Flutur i5"
#define X_DRIVER_TYPE  TMC2208_STANDALONE
#define Y_DRIVER_TYPE  TMC2208_STANDALONE
#define Z_DRIVER_TYPE  TMC2208_STANDALONE
#define E0_DRIVER_TYPE TMC2208_STANDALONE
#define EXTRUDERS 1
#define DEFAULT_NOMINAL_FILAMENT_DIA 1.75
#define TEMP_SENSOR_0 505
#define TEMP_SENSOR_1 0
#define TEMP_SENSOR_2 0
#define TEMP_SENSOR_3 0
#define TEMP_SENSOR_4 0
#define TEMP_SENSOR_5 0
#define TEMP_SENSOR_6 0
#define TEMP_SENSOR_7 0
#define TEMP_SENSOR_BED 505
#define TEMP_SENSOR_PROBE 0
#define TEMP_SENSOR_CHAMBER 0
#define TEMP_SENSOR_COOLER 0
#define TEMP_SENSOR_BOARD 0
#define TEMP_SENSOR_REDUNDANT 0
#define DUMMY_THERMISTOR_998_VALUE  25
#define DUMMY_THERMISTOR_999_VALUE 100
#if TEMP_SENSOR_IS_MAX_TC(0)
  #define MAX31865_SENSOR_OHMS_0      100 // (Ω) Typically 100 or 1000 (PT100 or PT1000)
  #define MAX31865_CALIBRATION_OHMS_0 430 // (Ω) Typically 430 for Adafruit PT100; 4300 for Adafruit PT1000
#endif
#if TEMP_SENSOR_IS_MAX_TC(1)
  #define MAX31865_SENSOR_OHMS_1      100
  #define MAX31865_CALIBRATION_OHMS_1 430
#endif
#if TEMP_SENSOR_IS_MAX_TC(2)
  #define MAX31865_SENSOR_OHMS_2      100
  #define MAX31865_CALIBRATION_OHMS_2 430
#endif
#if HAS_E_TEMP_SENSOR
  #define TEMP_RESIDENCY_TIME         7  // (seconds) Time to wait for hotend to "settle" in M109
  #define TEMP_WINDOW                  1  // (°C) Temperature proximity for the "temperature reached" timer
  #define TEMP_HYSTERESIS              3  // (°C) Temperature proximity considered "close enough" to the target
#endif
#if TEMP_SENSOR_BED
  #define TEMP_BED_RESIDENCY_TIME     7  // (seconds) Time to wait for bed to "settle" in M190
  #define TEMP_BED_WINDOW              1  // (°C) Temperature proximity for the "temperature reached" timer
  #define TEMP_BED_HYSTERESIS          3  // (°C) Temperature proximity considered "close enough" to the target
#endif
#if TEMP_SENSOR_CHAMBER
  #define TEMP_CHAMBER_RESIDENCY_TIME 10  // (seconds) Time to wait for chamber to "settle" in M191
  #define TEMP_CHAMBER_WINDOW          1  // (°C) Temperature proximity for the "temperature reached" timer
  #define TEMP_CHAMBER_HYSTERESIS      3  // (°C) Temperature proximity considered "close enough" to the target
#endif
#if TEMP_SENSOR_REDUNDANT
  #define TEMP_SENSOR_REDUNDANT_SOURCE    E1  // The sensor that will provide the redundant reading.
  #define TEMP_SENSOR_REDUNDANT_TARGET    E0  // The sensor that we are providing a redundant reading for.
  #define TEMP_SENSOR_REDUNDANT_MAX_DIFF  10  // (°C) Temperature difference that will trigger a print abort.
#endif
#define HEATER_0_MINTEMP   1
#define HEATER_1_MINTEMP   5
#define HEATER_2_MINTEMP   5
#define HEATER_3_MINTEMP   5
#define HEATER_4_MINTEMP   5
#define HEATER_5_MINTEMP   5
#define HEATER_6_MINTEMP   5
#define HEATER_7_MINTEMP   5
#define BED_MINTEMP        1
#define CHAMBER_MINTEMP    1
#define HEATER_0_MAXTEMP 275
#define HEATER_1_MAXTEMP 275
#define HEATER_2_MAXTEMP 275
#define HEATER_3_MAXTEMP 275
#define HEATER_4_MAXTEMP 275
#define HEATER_5_MAXTEMP 275
#define HEATER_6_MAXTEMP 275
#define HEATER_7_MAXTEMP 275
#define BED_MAXTEMP      85
#define CHAMBER_MAXTEMP  60
#define HOTEND_OVERSHOOT 15   // (°C) Forbid temperatures over MAXTEMP - OVERSHOOT
#define BED_OVERSHOOT    10   // (°C) Forbid temperatures over MAXTEMP - OVERSHOOT
#define COOLER_OVERSHOOT  2   // (°C) Forbid temperatures closer than OVERSHOOT
#define PIDTEMP           // See the PID Tuning Guide at https://reprap.org/wiki/PID_Tuning
#define PID_MAX  255      // Limit hotend current while PID is active (see PID_FUNCTIONAL_RANGE below); 255=full current
#define PID_K1     0.95   // Smoothing factor within any PID loop
    #define DEFAULT_Kp   52.65
    #define DEFAULT_Ki    7.57
    #define DEFAULT_Kd  91.62
#define MAX_BED_POWER 255 // limits duty cycle to bed; 255=full current
#define MAX_CHAMBER_POWER 255 // limits duty cycle to chamber heater; 255=full current
  #define PID_FUNCTIONAL_RANGE 10 // If the temperature difference between the target temperature and the actual temperature
#define PREVENT_COLD_EXTRUSION
#define EXTRUDE_MINTEMP 170
#define PREVENT_LENGTHY_EXTRUDE
#define EXTRUDE_MAXLENGTH 200
#define THERMAL_PROTECTION_HOTENDS // Enable thermal protection for all extruders
#define THERMAL_PROTECTION_BED     // Enable thermal protection for the heated bed
#define THERMAL_PROTECTION_CHAMBER // Enable thermal protection for the heated chamber
#define THERMAL_PROTECTION_COOLER  // Enable thermal protection for the laser cooling
#define USE_XMIN_PLUG
#define USE_ZMIN_PLUG
#define USE_YMAX_PLUG
#define ENDSTOPPULLUPS
#define X_MIN_ENDSTOP_INVERTING false // Set to true to invert the logic of the endstop.
#define Y_MIN_ENDSTOP_INVERTING false // Set to true to invert the logic of the endstop.
#define Z_MIN_ENDSTOP_INVERTING false // Set to true to invert the logic of the endstop.
#define I_MIN_ENDSTOP_INVERTING false // Set to true to invert the logic of the endstop.
#define J_MIN_ENDSTOP_INVERTING false // Set to true to invert the logic of the endstop.
#define K_MIN_ENDSTOP_INVERTING false // Set to true to invert the logic of the endstop.
#define U_MIN_ENDSTOP_INVERTING false // Set to true to invert the logic of the endstop.
#define V_MIN_ENDSTOP_INVERTING false // Set to true to invert the logic of the endstop.
#define W_MIN_ENDSTOP_INVERTING false // Set to true to invert the logic of the endstop.
#define X_MAX_ENDSTOP_INVERTING false // Set to true to invert the logic of the endstop.
#define Y_MAX_ENDSTOP_INVERTING false // Set to true to invert the logic of the endstop.
#define Z_MAX_ENDSTOP_INVERTING false // Set to true to invert the logic of the endstop.
#define I_MAX_ENDSTOP_INVERTING false // Set to true to invert the logic of the endstop.
#define J_MAX_ENDSTOP_INVERTING false // Set to true to invert the logic of the endstop.
#define K_MAX_ENDSTOP_INVERTING false // Set to true to invert the logic of the endstop.
#define U_MAX_ENDSTOP_INVERTING false // Set to true to invert the logic of the endstop.
#define V_MAX_ENDSTOP_INVERTING false // Set to true to invert the logic of the endstop.
#define W_MAX_ENDSTOP_INVERTING false // Set to true to invert the logic of the endstop.
#define Z_MIN_PROBE_ENDSTOP_INVERTING false // Set to true to invert the logic of the probe.
#define DEFAULT_AXIS_STEPS_PER_UNIT   { 80, 80, 600, 95.28 }
#define DEFAULT_MAX_FEEDRATE          { 2000, 2000, 100, 25 }
#define DEFAULT_MAX_ACCELERATION      { 600, 600, 200, 10000 }
#define DEFAULT_ACCELERATION          600    // X, Y, Z and E acceleration for printing moves
#define DEFAULT_RETRACT_ACCELERATION  1000    // E acceleration for retracts
#define DEFAULT_TRAVEL_ACCELERATION   600    // X, Y, Z acceleration for travel (non printing) moves
#define CLASSIC_JERK
  #define DEFAULT_XJERK 7.0
  #define DEFAULT_YJERK 7.0
  #define DEFAULT_ZJERK  0.3
#define DEFAULT_EJERK    5.0  // May be used by Linear Advance
#define NOZZLE_TO_PROBE_OFFSET { 10, 10, 0 }
#define PROBING_MARGIN 10
#define XY_PROBE_FEEDRATE (133*60)
#define Z_PROBE_FEEDRATE_FAST (4*60)
#define Z_PROBE_FEEDRATE_SLOW (Z_PROBE_FEEDRATE_FAST / 2)
#define Z_CLEARANCE_DEPLOY_PROBE   10 // (mm) Z Clearance for Deploy/Stow
#define Z_CLEARANCE_BETWEEN_PROBES  5 // (mm) Z Clearance between probe points
#define Z_CLEARANCE_MULTI_PROBE     5 // (mm) Z Clearance between multiple probes
#define Z_PROBE_LOW_POINT          -2 // (mm) Farthest distance below the trigger-point to go before stopping
#define Z_PROBE_OFFSET_RANGE_MIN -20
#define Z_PROBE_OFFSET_RANGE_MAX 20
#define X_ENABLE_ON 0
#define Y_ENABLE_ON 0
#define Z_ENABLE_ON 0
#define E_ENABLE_ON 0 // For all extruders
#define DISABLE_E               // Disable the extruder when not stepping
#define DISABLE_OTHER_EXTRUDERS   // Keep only the active extruder enabled
#define INVERT_X_DIR true
#define INVERT_Y_DIR false
#define INVERT_Z_DIR false
#define INVERT_E0_DIR true
#define INVERT_E1_DIR false
#define INVERT_E2_DIR false
#define INVERT_E3_DIR false
#define INVERT_E4_DIR false
#define INVERT_E5_DIR false
#define INVERT_E6_DIR false
#define INVERT_E7_DIR false
#define Z_HOMING_HEIGHT  5        // (mm) Minimal Z height before homing (G28) for Z clearance above the bed, clamps, ...
#define X_HOME_DIR -1
#define Y_HOME_DIR 1
#define Z_HOME_DIR -1
#define X_BED_SIZE 285
#define Y_BED_SIZE 300
#define X_MIN_POS 0
#define Y_MIN_POS -6 //van beda, ispred
#define Z_MIN_POS 0
#define X_MAX_POS X_BED_SIZE
#define Y_MAX_POS Y_BED_SIZE
#define Z_MAX_POS 300
#define MIN_SOFTWARE_ENDSTOPS
  #define MIN_SOFTWARE_ENDSTOP_X
  #define MIN_SOFTWARE_ENDSTOP_Y
  #define MIN_SOFTWARE_ENDSTOP_Z
  #define MIN_SOFTWARE_ENDSTOP_I
  #define MIN_SOFTWARE_ENDSTOP_J
  #define MIN_SOFTWARE_ENDSTOP_K
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

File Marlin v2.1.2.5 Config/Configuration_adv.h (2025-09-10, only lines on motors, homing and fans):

#define E0_AUTO_FAN_PIN -1
#define E1_AUTO_FAN_PIN -1
#define E2_AUTO_FAN_PIN -1
#define E3_AUTO_FAN_PIN -1
#define E4_AUTO_FAN_PIN -1
#define E5_AUTO_FAN_PIN -1
#define E6_AUTO_FAN_PIN -1
#define E7_AUTO_FAN_PIN -1
#define CHAMBER_AUTO_FAN_PIN -1
#define COOLER_AUTO_FAN_PIN -1
#define HOMING_BUMP_MM      { 5, 5, 5 }       // (linear=mm, rotational=°) Backoff from endstops after first bump
#define HOMING_BUMP_DIVISOR { 4, 4, 2 }       // Re-Bump Speed Divisor (Divides the Homing Feedrate)
#define MICROSTEP_MODES { 16, 16, 16, 16, 16, 16 } // [1,2,4,8,16]

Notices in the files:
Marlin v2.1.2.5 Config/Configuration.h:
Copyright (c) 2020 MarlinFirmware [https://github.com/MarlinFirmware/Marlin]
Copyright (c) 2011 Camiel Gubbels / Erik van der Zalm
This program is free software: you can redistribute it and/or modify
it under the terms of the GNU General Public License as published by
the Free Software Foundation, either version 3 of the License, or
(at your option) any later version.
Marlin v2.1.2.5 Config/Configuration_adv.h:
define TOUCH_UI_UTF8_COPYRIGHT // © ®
